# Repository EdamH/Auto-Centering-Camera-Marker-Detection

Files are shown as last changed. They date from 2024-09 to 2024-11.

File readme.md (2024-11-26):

# Development of an Intelligent Camera System for the Detection & Automatic Centering of Markers

## 1- Brief Description : 

The motivation behind this project stems from the need to enhance the safety, efficiency,
and accuracy of power line inspections. Traditional methods, which often involve
manned helicopters, are not only costly and time-consuming but also pose significant
risks to human operators. By automating the detection and centering processes
using advanced algorithms, embedded systems, and wireless communication,
this project aims to offer a more reliable and scalable solution that can adapt to various
geographical and environmental conditions.

## 2- Requirements and coverage :

- [x] The system must detect markers in images and their offset from the desired position (e.g., using an algorithm like Canny edge detection)
- [x] The system must include an embedded controller to correct the camera position across all three axes (e.g., using servo motors)
- [x] The system must support wireless communication of the original image and correction parameters (e.g., using Bluetooth Low Energy boards)
- [x] The system must implement energy management for all components (e.g., utilizing solar panels or rechargeable batteries)
- [x] The system must feature an Android app to display images and correction parameters.
- [x] The system must be printed onto a PCB card.
- [x] The camera support allowing the camera to turn around all three axes must be modeled and printed.

## 3- The Technological Stack :

Currently, the project uses the following technologies:

- Raspberry Pi 4 (single-board computer)
- ESP32 (Wi-Fi and Bluetooth microcontroller)
- Power Management Unit (PMU)
- Pi Camera (camera module for Raspberry Pi)
- Batteries and Solar Panels (for power management)
- Altium Designer (for PCB design)
- Pi Imager (for creating Raspberry Pi SD cards)
- Arduino IDE (for microcontroller programming)
- VNC Viewer (for remote desktop control)
- Fusion 360 (for 3D design and manufacturing)
- Blender (for 3D graphics and modeling)
- Python (for computer vision algorithm development)
- VS Code (source code editor)
- OpenCV (computer vision library)
- Flutter (UI development kit)
- Dart (for mobile app development )

## 4- Solution Architecture :

### 4.1- Hardware Architecture

#### Overview

##### Data Flow
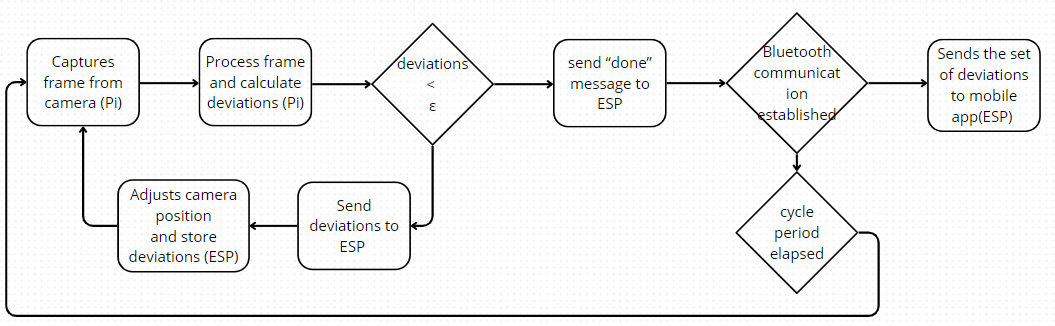
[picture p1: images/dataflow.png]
Data flow
  
- The data flow diagram represents the core process of the project. The process begins with the camera capturing a frame, which is processed by the Raspberry Pi 4 using a computer vision algorithm. This algorithm calculates deviations along three axes.
- These deviations are compared against a predefined epsilon value. If any deviation exceeds the epsilon threshold, the values are transmitted to the ESP32.
- The ESP32 stores the deviations and commands the servo motors to adjust the camera’s position to the desired alignment. 
- This cycle repeats until all deviations fall within the epsilon threshold.
- When the system meets this condition, it waits for the next cycle to begin.
- If a Bluetooth connection is established with a mobile device, the set of deviations is transmitted to the mobile application for logging and monitoring.

##### Current Flow
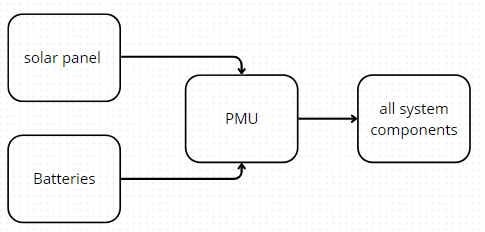
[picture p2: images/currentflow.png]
Current flow
  
- The current flow diagram shows the power distribution in the project.
- Batteries provide power to the entire system, managed by the Power Management Unit (PMU).
- The PMU ensures stable voltage and current delivery to all components.
- It also manages the battery charging process using solar panels, while protecting against overcharging, overdischarging, and short circuits, ensuring safe and efficient operation of the system.

## 4.2- Software Architecture

### Computer Vision
- The approach overview is depicted in Figure 3.3, which outlines the steps taken to provide the necessary offsets to the system.
- The camera captures frames, which are processed by the computer vision algorithm on the Raspberry Pi to calculate deviations from the desired position across three axes.

<div style="text-align: center;">
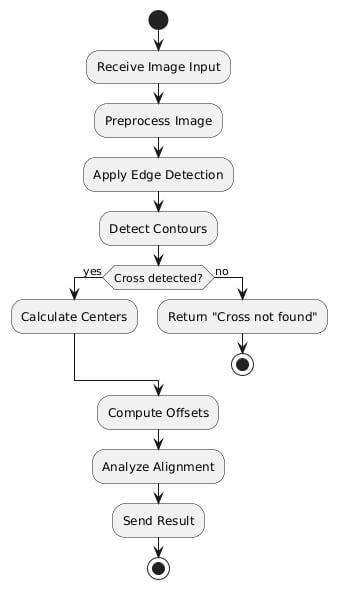
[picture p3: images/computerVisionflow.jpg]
Computer Vision
    
</div>

## 3D Modeling :

This section highlights the various components we modeled for our solution. Since the mechanical aspect of the project was not the main focus, we do not go into detail on the technical drawings.

- **Figure 4.2.1** – Full Gimbal: A complete view of the gimbal designed to hold the camera.
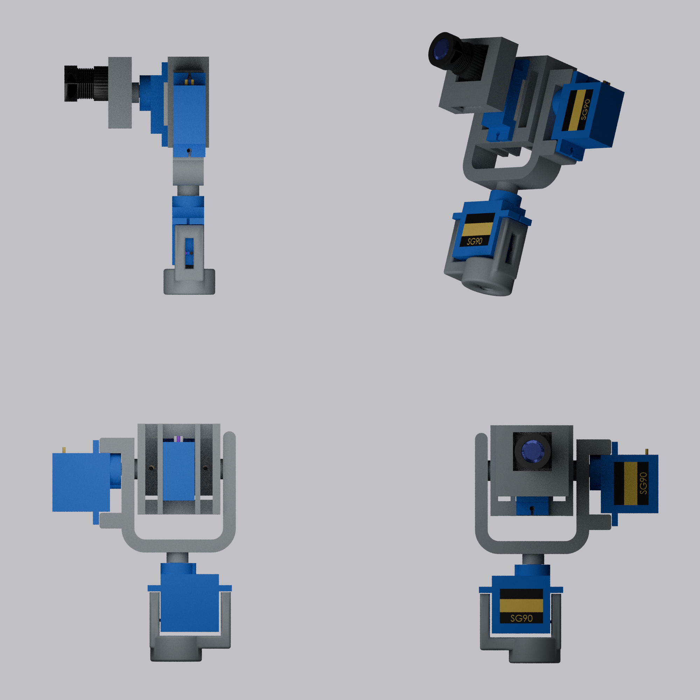
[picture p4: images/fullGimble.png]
Full Solution
  
- **Figure 4.2.2** – Unmounted Full Gimbal: A view of the gimbal when disassembled.
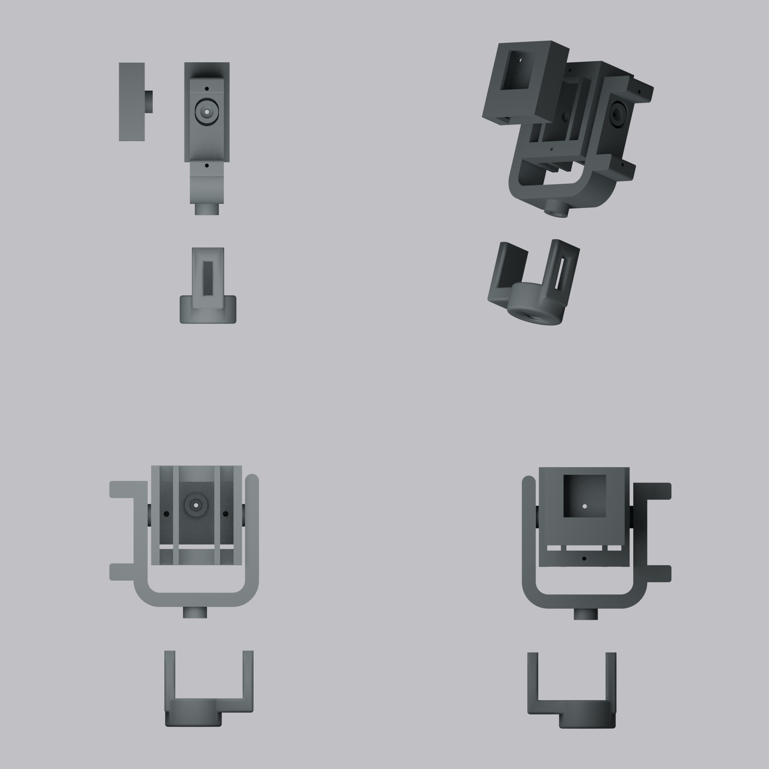
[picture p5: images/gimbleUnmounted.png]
3D model
  
- **Figure 4.2.3** – Battery Holder: A custom-designed holder for securing the batteries that power the system.
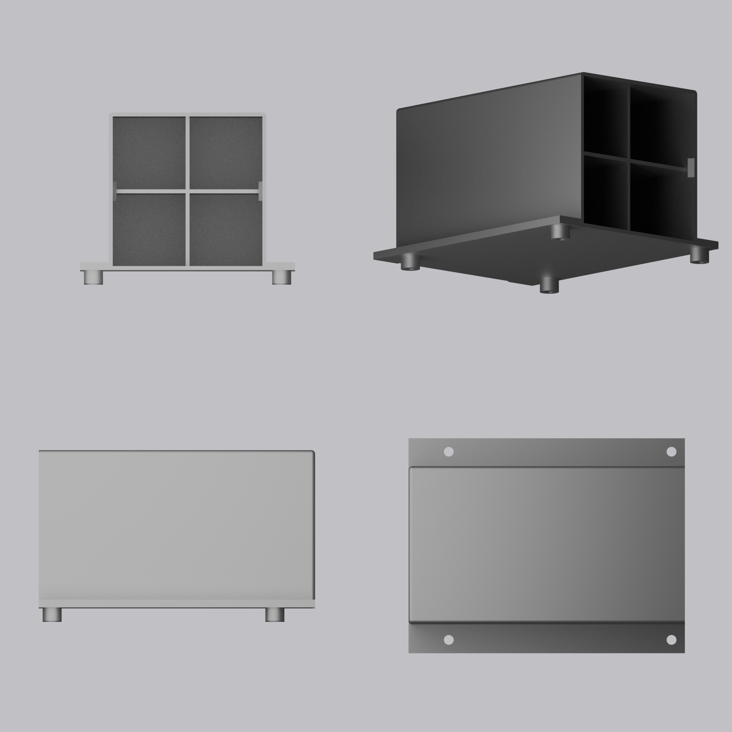
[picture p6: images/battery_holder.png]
Battery Holder
  

## 5- Embedded System :

## Strategies for Power Efficiency

### Manual Sleep Mode Implementation
The Raspberry Pi 4 does not have a built-in sleep mode, so a manual solution was implemented. This involves powering on the Raspberry Pi, performing calculations and camera alignment, scheduling the next boot, and then shutting down the system. This approach allows a 2.4 Ah battery to support approximately 13 hours of operation, effectively doubling the battery life.

### Integrating ESP8266 to Manage Raspberry Pi Power Usage
To further optimize power consumption, the ESP8266 was integrated as a secondary microcontroller. It consumes roughly one-tenth of the power used by the Raspberry Pi in power-off mode, allowing the ESP8266 to control the power to the Raspberry Pi and extending battery life to approximately 60 hours with the same battery.

## Raspberry Pi Issues and Implemented Solutions

### Instability in PWM Signal
The PWM signal generated by the Raspberry Pi was unstable, causing jitter in the servos. The ESP8266 was used to drive the servos, providing a more stable PWM signal.

### Transition to ESP32 for Bluetooth Communication
Bluetooth communication was challenging with the Raspberry Pi, so the ESP32 was chosen for its integrated Bluetooth capabilities and lower power consumption, enabling efficient data exchange with the mobile app.

## Design of Power Management Unit

### Schematic
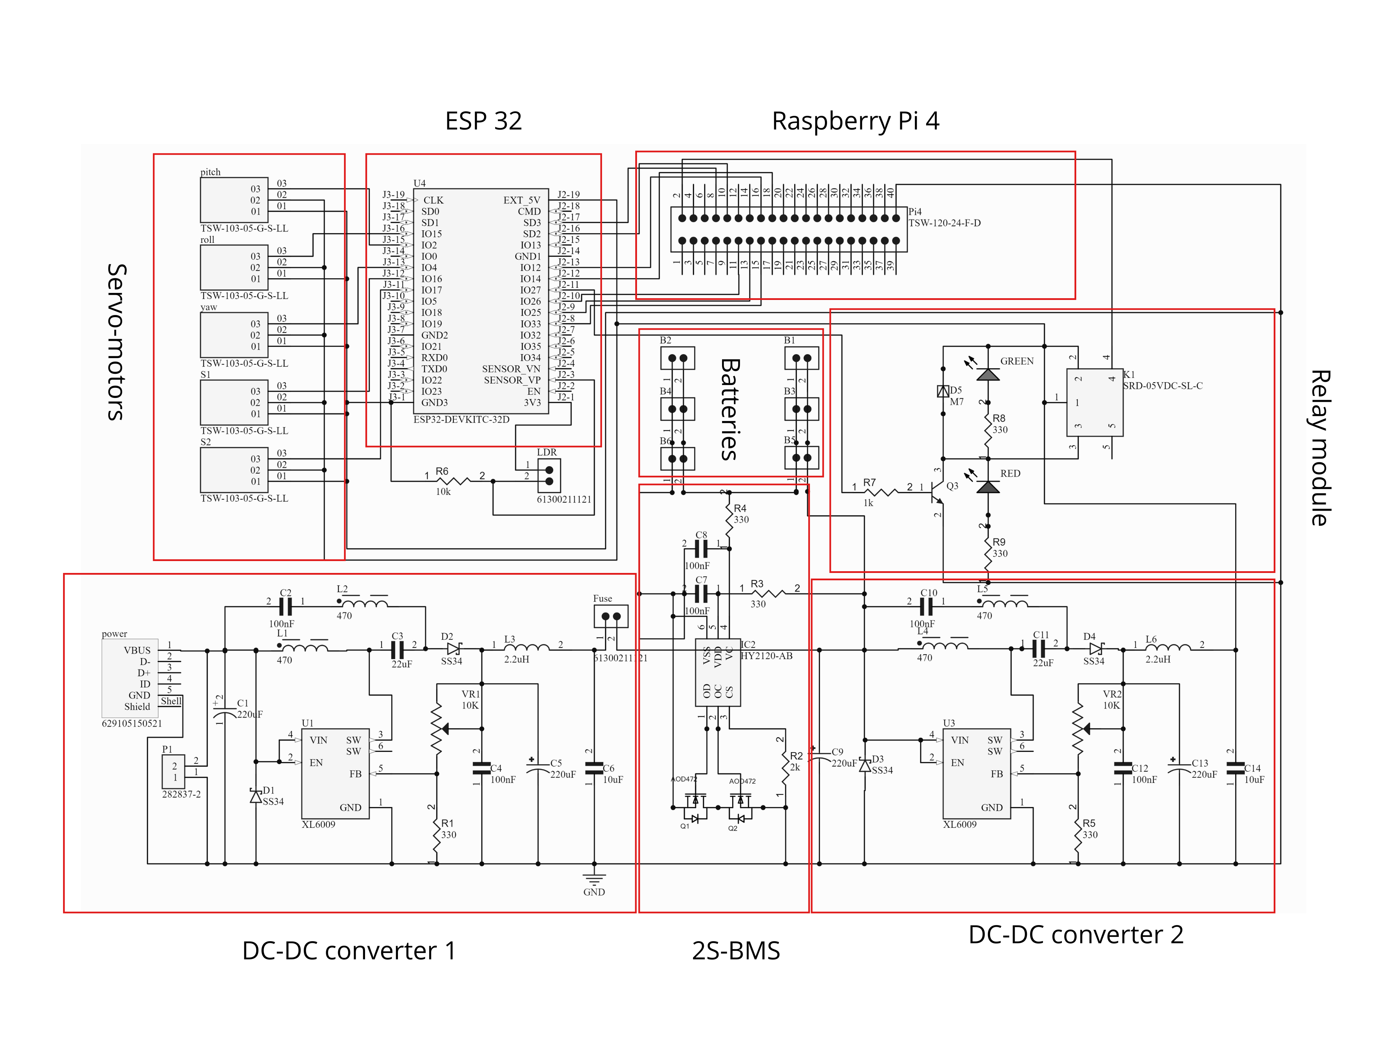
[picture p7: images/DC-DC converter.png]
Power Management Schematic


The schematic includes:
- **DC-DC Converter**: Stabilizes charging voltage at 8.4V and supplies a consistent 5V to the Raspberry Pi and other components.
- **Battery Management System (BMS)**: Controls charging and discharging, prevents overcharging and overdischarging, and ensures voltage balancing.

### PCB
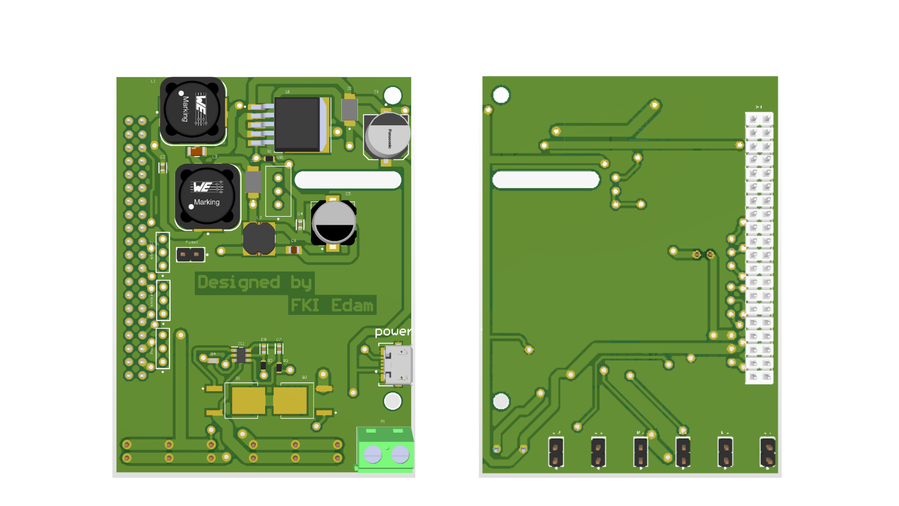
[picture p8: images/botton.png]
Bottom PCB
  
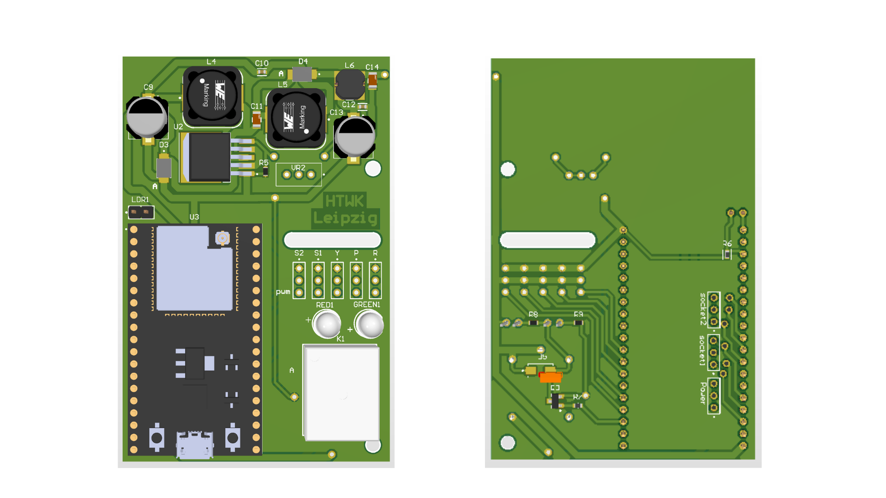
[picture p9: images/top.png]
Top PCB
  
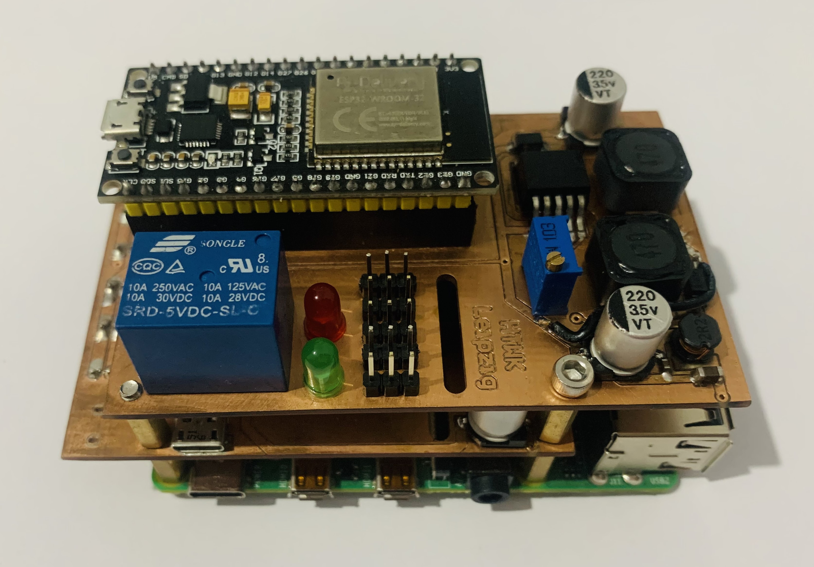
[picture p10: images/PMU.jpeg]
Manufactured PCB


## Energy Consumption

### System Cycle
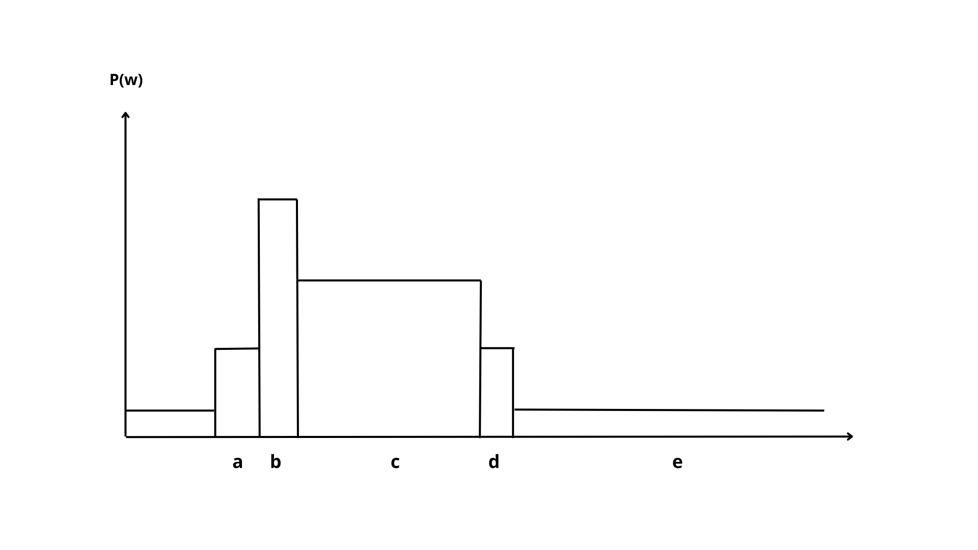
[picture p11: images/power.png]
Power Consumption Cycle


| Component | Energy Consumption | Duration |
|---|---|---|
| Raspberry Pi 4 | At Shut Down: 250mA | 60s |
| | At Processing: 600mA | |
| | At Booting: 1A | |
| ESP32 | At Idle: 20mA | 15 min |
| | At Processing: 80mA | |
| PMU | 20mA | 15 min |
| Servo Motor | 0.1A | 4s |
| Camera | 0.1A | 4s |

### Battery Life
Average power consumption calculated to be approximately 0.7W, resulting in an autonomy of 25h 22min with the existing battery setup. A more powerful solar panel will be needed for full recharging.

### Solar Panel
Initially used a 50W, 17V solar panel, but switched to smaller solar cells for size efficiency while maintaining sufficient power for battery recharging.

## Communication Between ESP-32 and Raspberry Pi 4

### Explored Protocols
- **SPI**: High data rate, master/slave configuration.
- **UART**: Simple, peer-to-peer communication.
- **I2C**: Multi-master/slave with two lines.
- **MQTT**: Lightweight, suitable for IoT applications.

### Selected Protocol: Serial (UART)
After evaluation, UART was chosen for its simplicity and sufficient data rate, allowing either device to initiate communication.

### Implementation Details
#### Hardware Setup
- **UART Communication Lines**: 
  - Pi TX Pin → ESP32 UART1 RX Pin
  - Pi RX Pin → ESP32 UART1 TX Pin
- **Interrupt Line**: 
  - Pi GPIO Pin → ESP32 GPIO Pin
- **Ground Connection**: 
  - GND pins connected for a common ground reference.

#### Protocol Workflow
<div style="text-align: center;">
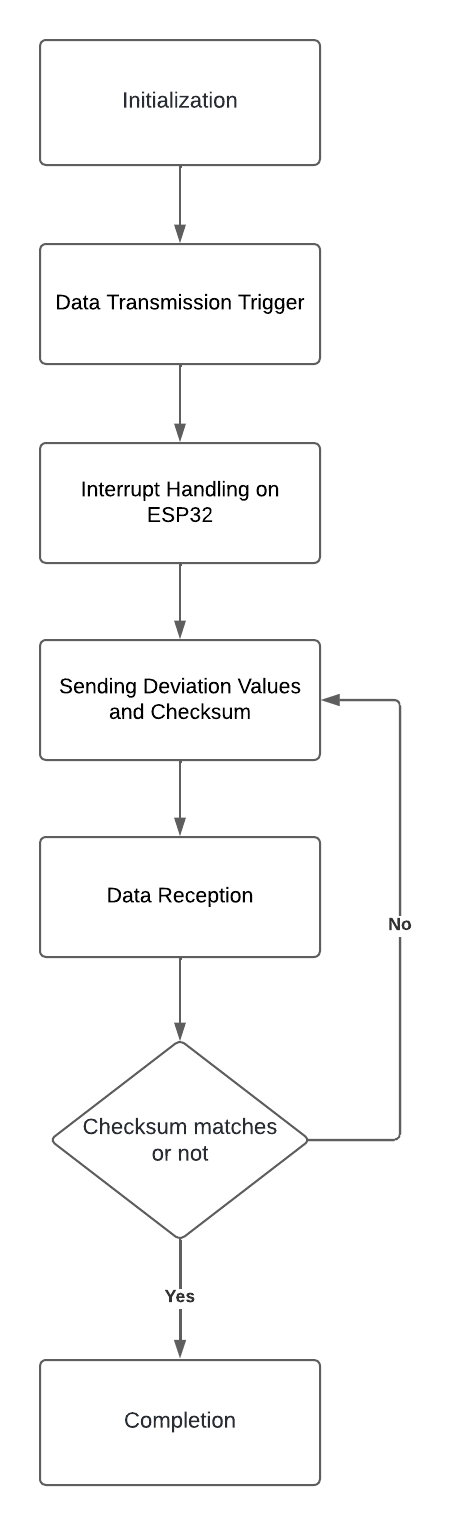
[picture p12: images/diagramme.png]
Protocol Workflow
    
</div>

The communication involves initialization, data transmission triggers, and acknowledgment of received data between the Raspberry Pi and ESP32.

## 6- Computer Vision :

## Cross Detection

### Approach Overview
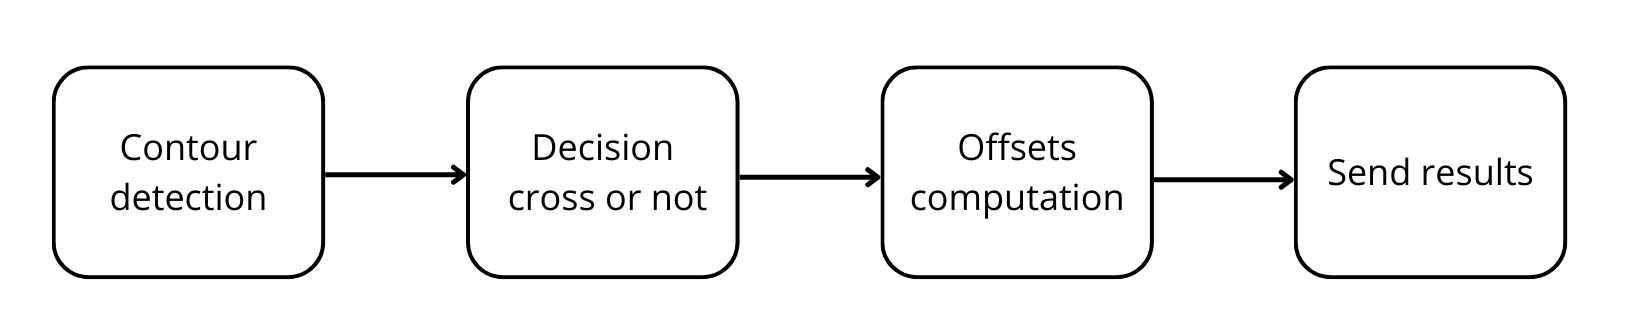
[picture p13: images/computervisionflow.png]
Approach Overview


### Contour Detection
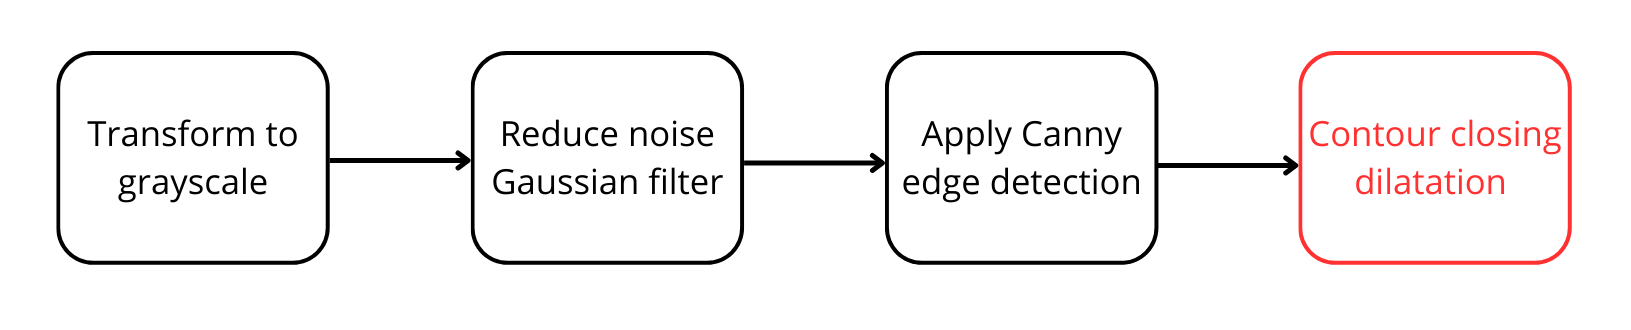
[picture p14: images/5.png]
Contour Detection Pipeline


In this step, the image is loaded in grayscale to simplify data and enhance edge detection. A Gaussian blur filter is applied to reduce noise, followed by Canny edge detection with optimal threshold values to filter weak edges while retaining strong ones. Finally, contours are extracted from the edge-detected image.

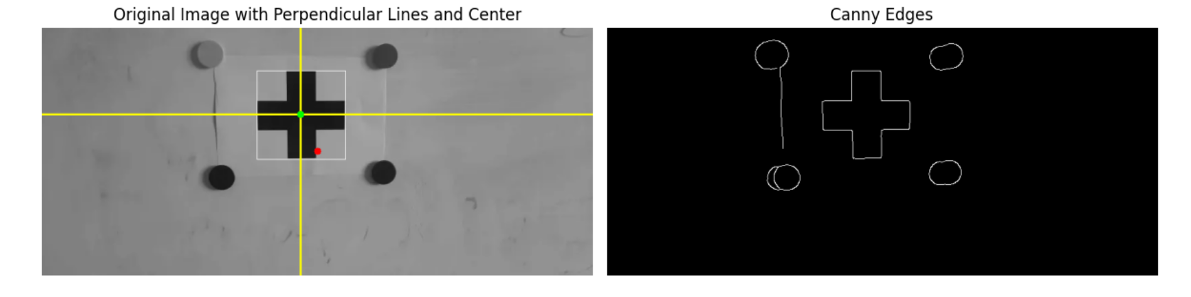
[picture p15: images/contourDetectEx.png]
Example of Cross Detection


To address discontinuities in the contours, dilation is applied to the edge-detected image, expanding the boundaries of detected edges.

### Decision About the Cross
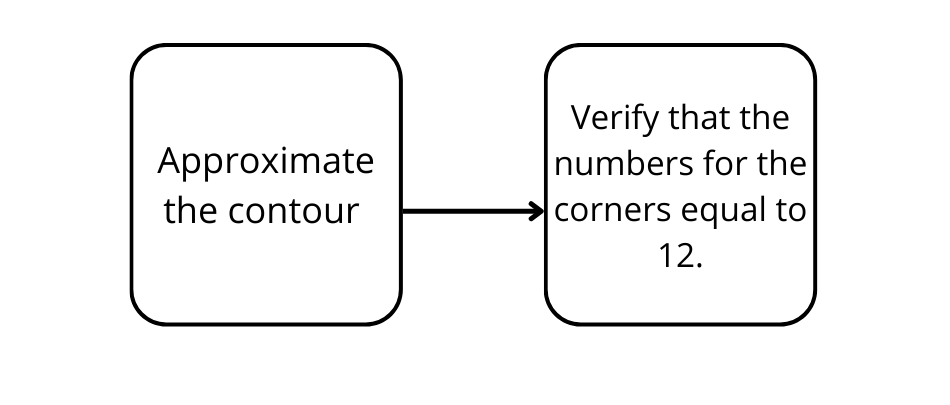
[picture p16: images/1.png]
Decision Pipeline


The detected contours are simplified and approximated to polygons with fewer vertices using a specified epsilon parameter for accuracy. Contours with 12 corners are filtered to identify the cross shape, and a bounding box is determined to convert offsets from pixels to meters.

### Offsets Computation
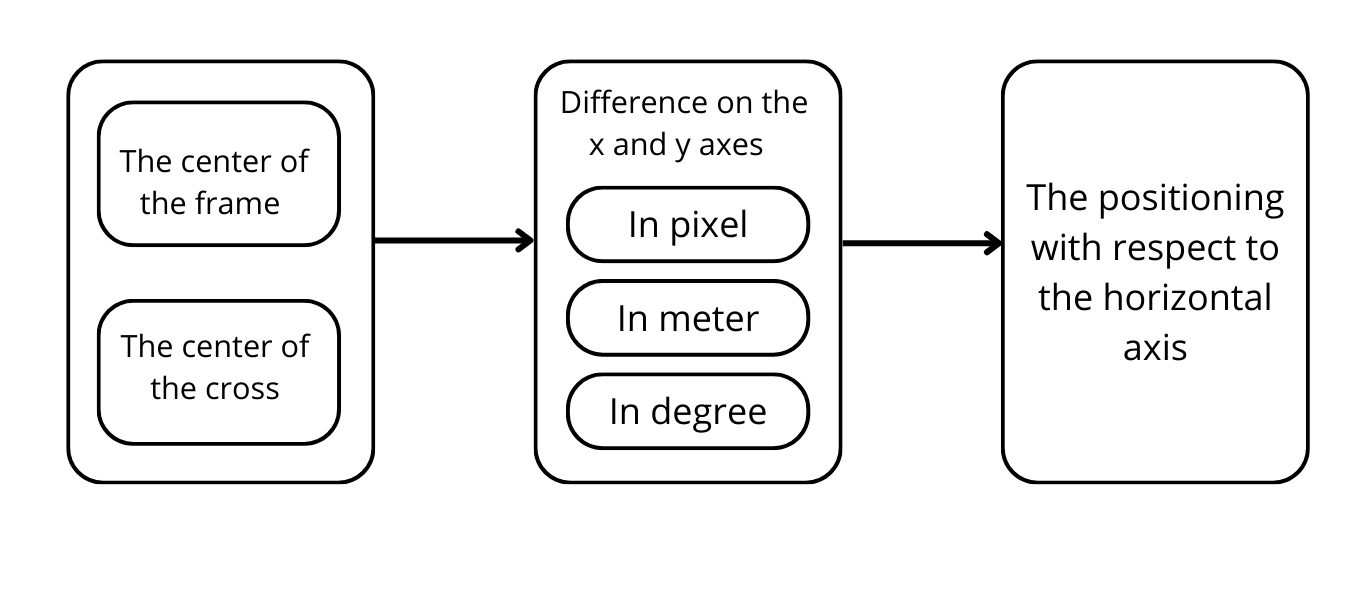
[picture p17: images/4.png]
Offsets Computation Pipeline


Offsets for the servo motors are calculated by determining the centers of the image and the cross. The difference in pixel coordinates on the x and y axes is computed. Using the cross width, a ratio for converting pixel measurements to physical dimensions is derived, allowing the extraction of angles for servo-motor adjustments.

Additionally, the alignment of the cross is considered by calculating its deviation from the horizontal axis by drawing a line between the closest detected corners and calculating the angle relative to the axis.

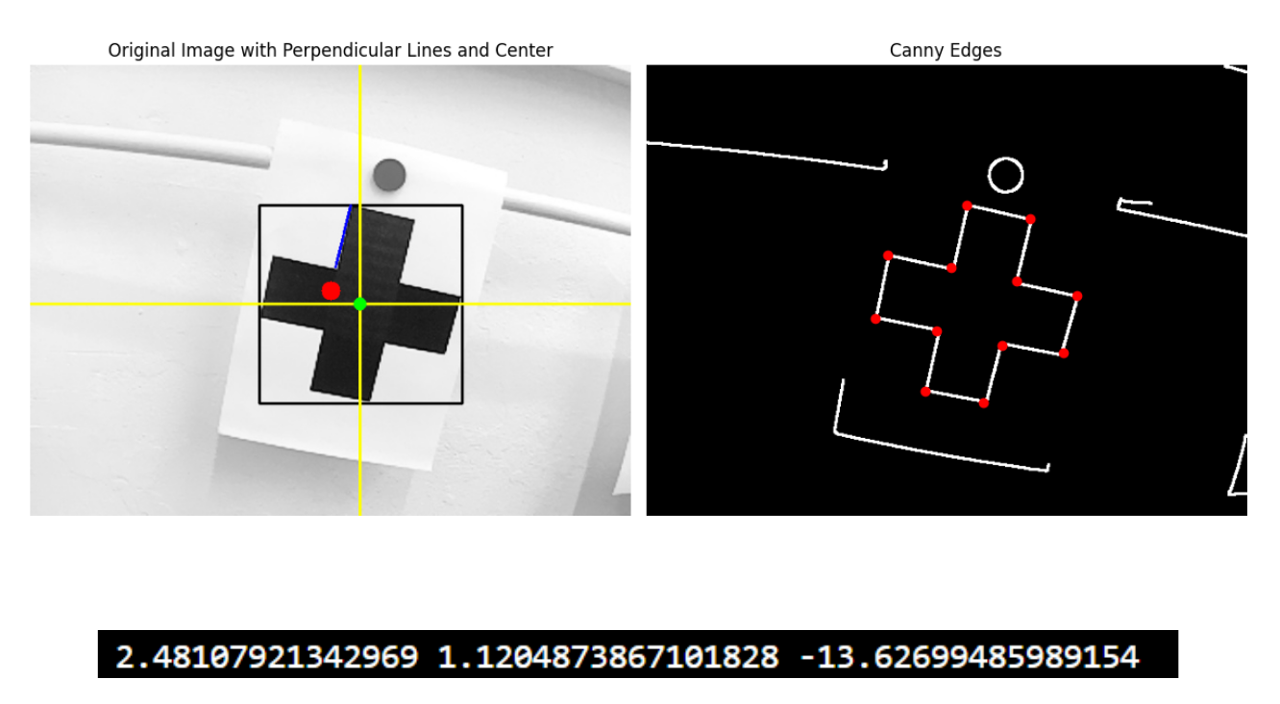
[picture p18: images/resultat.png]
Example of Result


### Approach Limits
The algorithm can theoretically detect a cross with an opacity level of 6%, but in practice, it achieves around 25%.

## Mathematical Approach :

### Overview
Let (X, Y, Z) be the orthonormal reference attached to the camera, where Z is vertical and X points at the detected object. The orientations the camera must adjust to center the detected object are represented as θX, θY, and θZ.

The algorithm follows these steps:
1. The distance D between the camera and the detected object (cross or pole) is input.
2. The width of the item in pixels is computed to approximate the pixel-to-meter ratio.
3. Offsets along the vertical and horizontal axes are calculated, yielding rotations θZ and θY around the Z and Y axes.
4. Rotation along the θX axis is determined by comparing the object's orientation relative to the horizontal axis.

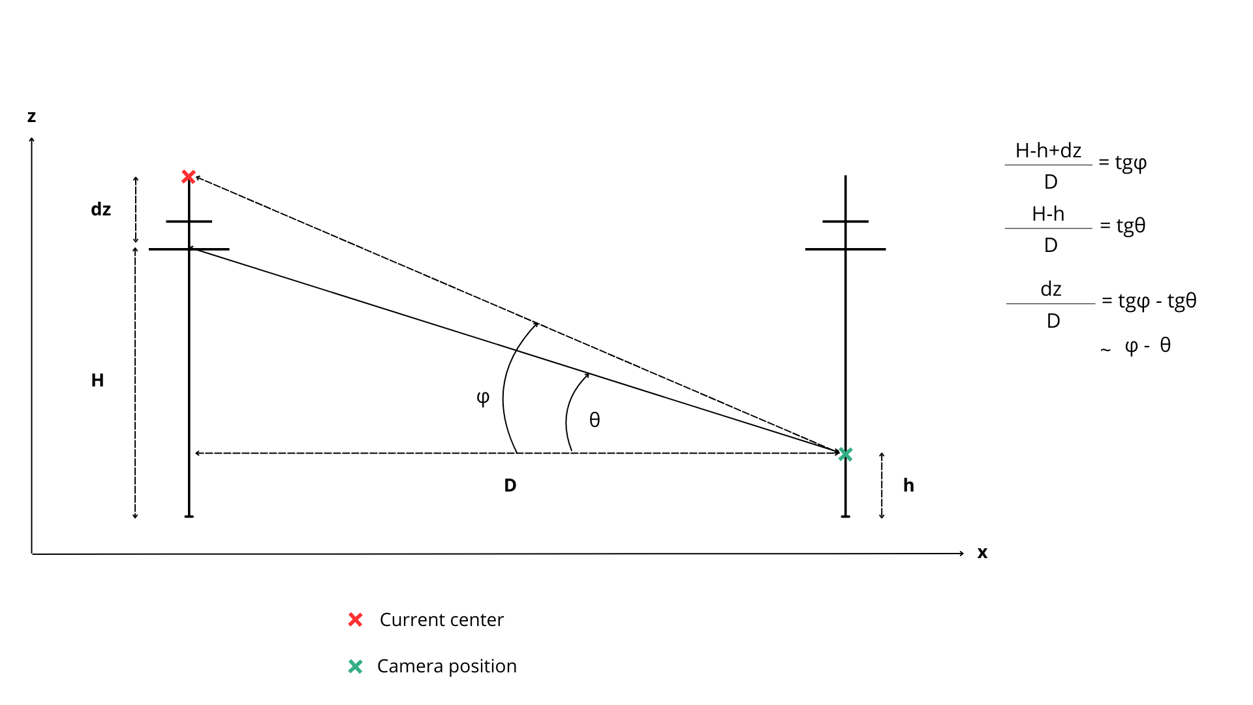
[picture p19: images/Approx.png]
Visual Representation of the Problem for θY


### Validity of the Approximation
To reduce computational load, the approximation tan(θ) ≈ θ is used when θ approaches 0. Analysis shows that the error is under 0.01 for θ < 0.31 and under 0.1 for θ < 0.63, ensuring that deviations remain manageable for the project's conditions.

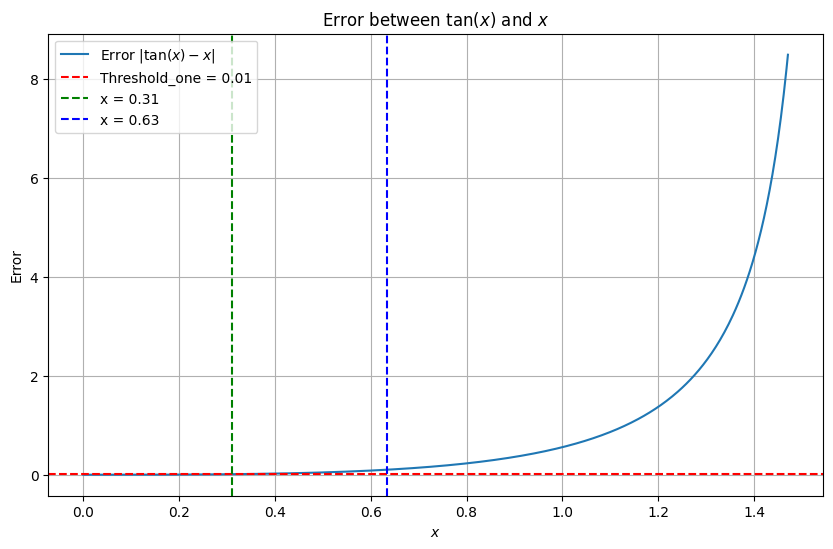
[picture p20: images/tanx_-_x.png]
Absolute Error |tan(θ) - θ|


## Bluetooth Communication for Mobile Application :

### Bluetooth Overview
Bluetooth is a wireless communication protocol designed for short-range data exchange between devices. Operating in the 2.4 GHz ISM band, it supports both point-to-point and point-to-multipoint connections. Bluetooth is widely used in consumer electronics for applications such as wireless audio, file transfers, and peripheral connections.

### Use Case and Implementation
In this system, Bluetooth facilitates communication between the ESP-32 and a mobile application, allowing users to interact via smartphones. Key features include remote control, status monitoring, and notifications.

The ESP-32 is configured to operate in Bluetooth Low Energy (BLE) mode, chosen for its low power consumption, essential for maintaining battery life in mobile applications. The mobile application connects to the ESP-32, enabling command transmission and real-time updates.

This wireless communication layer significantly enhances user experience, providing a convenient and accessible interface for system interaction without physical connections.

### Mobile Application
The mobile application is developed using Flutter and Dart, offering a cross-platform solution for both Android and iOS. Flutter enables the creation of visually appealing, high-performance interfaces, while Dart provides flexibility for handling Bluetooth communication and real-time data processing. This combination ensures a responsive and seamless user experience.

For Bluetooth communication, the SerialBT library is implemented on the ESP-32, providing a reliable method for data transmission between the system and the mobile app. SerialBT supports Bluetooth Classic profiles, ensuring compatibility and stability. This setup allows the ESP-32 to transmit real-time data, including cycle details and measurement offsets, directly to the app.

Once a stable Bluetooth connection is established, the system enters a critical phase where real-time data from the current cycle is transmitted. The ESP-32 provides detailed cycle information, including offsets, measurement indices, and current positions.

The mobile app processes incoming data to compute and display precise timestamps for each measurement, calculating the difference between the current time and the start of the cycle. This allows for accurate iteration through remaining measurements and the creation of a timeline.

In addition to real-time data presentation, the app generates a histogram visualizing the distribution of measurements over time. This provides users with accurate, time-stamped information and insights into the temporal distribution of measurements within each cycle.

The user interface prioritizes clarity and usability, focusing on presenting essential data in an intuitive format.

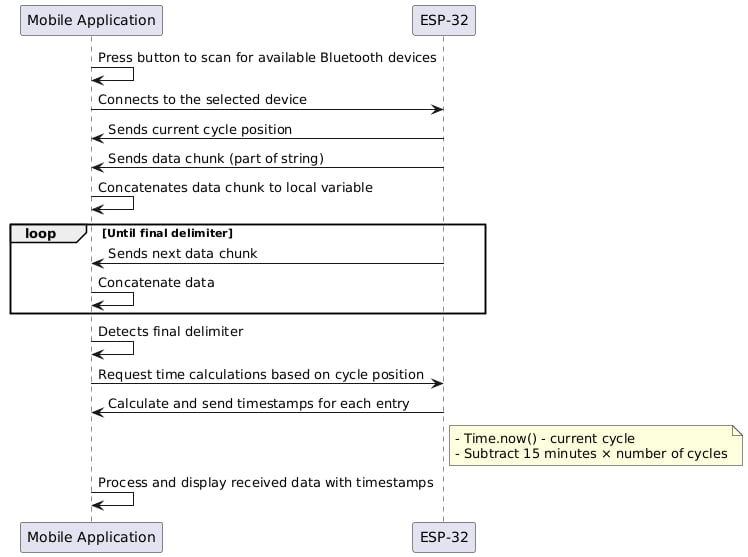
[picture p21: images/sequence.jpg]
Bluetooth Sequence


### Screenshots of the Application
<div style="display: flex; justify-content: space-around;">
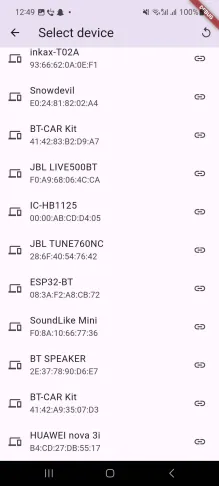
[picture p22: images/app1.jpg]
First Page
    
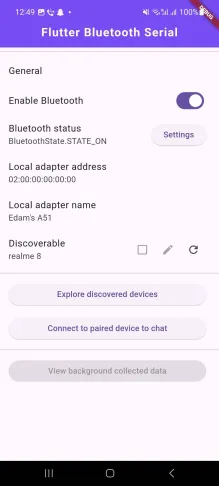
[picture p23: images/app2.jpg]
Paired Devices
    
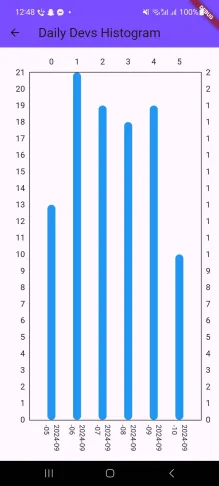
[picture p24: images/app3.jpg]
Measurements
    
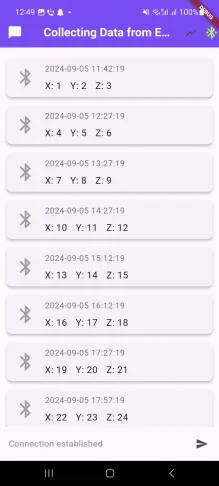
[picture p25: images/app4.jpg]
Histogram
    
</div>

## Collaborators
<a href="https://https://github.com/EdamH/Auto-Centering-Camera-Marker-Detection/graphs/contributors">
    
  
</a>

# Feel free to contribute!

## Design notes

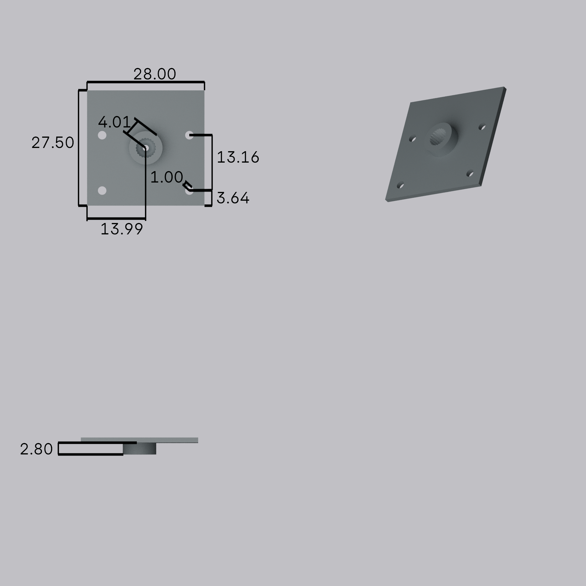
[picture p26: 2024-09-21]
images/cameraCaseRear.png

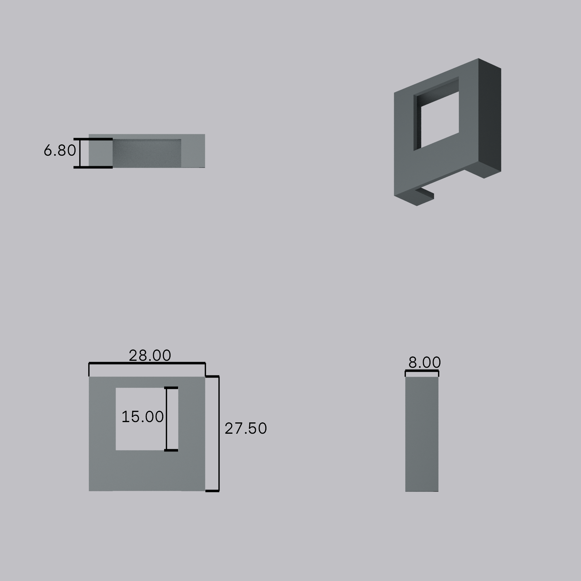
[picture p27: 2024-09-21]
images/cameraCase.png

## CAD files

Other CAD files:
3D Model/Cover v1.f3d
3D Model/Spacer v2.f3d
3D Model/battery_holder v3.f3d

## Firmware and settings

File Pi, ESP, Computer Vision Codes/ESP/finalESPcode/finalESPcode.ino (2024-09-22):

#include <HardwareSerial.h>  // Library to use hardware serial communication
#include <ESP32Servo.h>      // Library to control servos on ESP32
#include "BluetoothSerial.h" // Library for Bluetooth communication

BluetoothSerial SerialBT;    // Bluetooth object
String device_name = "ESP32-BT"; // Bluetooth device name

int Sample_number = 0;       // Counter for the number of samples processed
int t_cycle = 900000;        // Time cycle (15 minutes) in milliseconds

long tic = millis();         // Start time of the cycle

String dataset;              // String to store dataset (servo positions)

bool a = 1, b = 0, c = 0;    // Flags for the power-off sequence
long st;                     // Start time for power-off
int d;                       // Time remaining after power-off

// Pin definitions
#define relay 33             // Relay control pin (used to power Pi4)
#define s_interrupt 25       // Interrupt pin for servo control
#define p_interrupt 14       // Interrupt pin for power control

// Pins for hardware serial communication
#define RX 9
#define TX 10

Servo servo1, servo2, servo3; // Servo objects

// Initial servo positions
int X = 100, Y = 90, Z = 80;  

bool calculating = 1;        // Flag to indicate if calculations are ongoing
int delta = 0;               // Time spent in a cycle

HardwareSerial HSerial(1);   // Hardware serial object (for UART1)

volatile bool servo = false; // Flag set by the interrupt for servo control
volatile bool power = false; // Flag set by the interrupt for power control

// Interrupt handler for servo control
void IRAM_ATTR servo_write() {
  servo = true;  // Set a flag to indicate the servo interrupt event
}

// Interrupt handler for power control
void IRAM_ATTR power_off() {
  power = true;  // Set a flag to indicate the power interrupt event
}

void setup() {
  SerialBT.begin(device_name);         // Initialize Bluetooth with the device name
  pinMode(relay, OUTPUT);              // Set relay pin as output
  attachInterrupt(p_interrupt, power_off, RISING); // Attach interrupt for power control
  attachInterrupt(s_interrupt, servo_write, RISING); // Attach interrupt for servo control
  Serial.begin(115200);                // Initialize serial communication
  HSerial.begin(9600, SERIAL_8N1, RX, TX); // Initialize hardware serial for communication

  // Setup servos with a 50 Hz PWM signal and attach them to corresponding pins
  servo1.setPeriodHertz(50);
  servo1.attach(17, 550, 2500);        // Attach servo1 to pin 17
  servo2.setPeriodHertz(50);
  servo2.attach(16, 550, 2500);        // Attach servo2 to pin 16
  servo3.setPeriodHertz(50);
  servo3.attach(5, 550, 2500);         // Attach servo3 to pin 5

  // Write initial servo positions
  servo1.write(X);
  servo2.write(Y);
  servo3.write(Z);

  Serial.println(millis() - tic);      // Print time since the start of the program
}

void loop() {
  // If the system is in calculating mode, process servo adjustments
  if (calculating) {
    digitalWrite(relay, HIGH);         // Turn on the relay to power external devices

    // Check if the servo interrupt flag was set
    if (servo) {
      // Check if data is available on the hardware serial
      if (HSerial.available()) {
        Serial.println("receiving");
        String data = HSerial.readStringUntil('\n');  // Read incoming data until newline character
        int ang1 = 0, ang2 = 0, ang3 = 0, s = 0;      // Variables for servo angles and checksum
        Serial.println(data);

        // Parse the angles and checksum from the received data
        sscanf(data.c_str(), "%d,%d,%d,%d", &ang1, &ang2, &ang3, &s);

        Serial.print("servoN°1=");
        Serial.println(ang1);
        Serial.print("servoN°2=");
        Serial.println(ang2);
        Serial.print("servoN°3=");
        Serial.println(ang3);

        // Check the integrity of the received data
        int h = ang1 + 2 * ang2 + 3 * ang3;
        if (h - s == 0) { // If checksum is correct
          // Adjust servo positions
          X = X - ang1;
          Y = Y - ang2;
          Z = Z - ang3;

          Serial.print("x=");
          Serial.println(X);
          Serial.print("Y=");
          Serial.println(Y);
          Serial.print("Z=");
          Serial.println(Z);

          // Update servo positions if within valid range
          if (X > 60) {
            servo1.write(X);
          } else {
            Serial.println("x<60");
          }

          servo2.write(Y);

          if (Z > 60) {
            servo3.write(Z);
          } else {
            Serial.println("z<60");
          }

          // Send acknowledgment to the sender
          HSerial.println("received");
          Sample_number++;

          // Update dataset with the new positions
          String rotation = "";
          if (dataset.length() == 0) {
            rotation = String(X) + "," + String(Y) + "," + String(Z) + "\r";
          } else {
            rotation = "|" + String(X) + "," + String(Y) + "," + String(Z) + "\r";
          }
          dataset = dataset + rotation;

          // Clear the input buffer
          HSerial.readStringUntil('\n');
        } else {  // If checksum is incorrect
          HSerial.println("resend");
        }
      } else {  // If no serial data is available
        Serial.println("serial not available");
        HSerial.println("resend");
      }

      servo = false;  // Reset the servo interrupt flag
      HSerial.readStringUntil('\n');  // Clear any remaining data
    }

    // Check if the power interrupt flag was set
    if (power) {
      Serial.println("shutting down");
      calculating = 0;  // Stop calculations
      if (a) {          // First stage of power-off sequence
        st = millis();
        a = 0;
        b = 1;
      }
      if (b) {          // Wait for 4 seconds before powering off
        if (millis() - st >= 4000) {
          digitalWrite(relay, LOW);  // Turn off the relay to cut power
          delta = millis() - tic;    // Calculate the time spent in this cycle
          Serial.print("delta =");
          Serial.println(delta);
          d = t_cycle - delta;       // Calculate the remaining time for the cycle
          b = 0;
          c = 1;
          st = millis();
        }
      }
      if (c) {          // Wait for the remaining cycle time before restarting
        if (millis() - st >= d) {
          calculating = 1;  // Resume calculations after the cycle
          power = false;    // Reset the power interrupt flag
        }
      }
    }

    // Bluetooth communication: check if data is received via Bluetooth
    if (SerialBT.available()) {
      String incomingData = SerialBT.readStringUntil('\n');
      incomingData.trim();
      Serial.println("Received: " + incomingData);

      // If the received data is "a", send the elapsed time and dataset
      if (incomingData == "a") {
        long t = millis() - tic;  // Calculate the elapsed time
        Serial.println(t);
        String msg = String(t) + "#";  // Send the time

        int len = msg.length();
        char byteArray[len + 1];
        msg.getBytes((unsigned char*)byteArray, len + 1);
        SerialBT.write((uint8_t*)byteArray, len);
        delay(50);

        // Send the dataset of servo rotations
        msg = dataset + "\r";
        len = msg.length();
        char byteArray1[len + 1];
        msg.getBytes((unsigned char*)byteArray1, len + 1);
        SerialBT.write((uint8_t*)byteArray1, len);
      }
    }
  }
}

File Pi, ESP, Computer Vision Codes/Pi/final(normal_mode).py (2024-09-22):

import os
import cv2
import math
import numpy as np
from time import sleep
from itertools import combinations
from picamera2 import Picamera2
import random
import RPi.GPIO as GPIO
import matplotlib.pyplot as plt
import serial

epsilon=1 #the minimum deviatu=ion that can be made by servo-motors

# Initialize a flag to check if data needs to be resent
resend = False

# Initialize the serial connection for communication with another device
ser = serial.Serial('/dev/ttyS0', 9600, timeout=1)

# Set up GPIO pins for controlling hardware (e.g., servos)
GPIO.setmode(GPIO.BCM)
GPIO.setwarnings(False)
GPIO.setup(23, GPIO.OUT)  # Pin for sending data
GPIO.setup(24, GPIO.OUT)  # Pin for power control

def send(ang1, ang2, ang3):
    """
    Send the angles as a formatted message over serial communication.
    """
    message = f"{ang1},{ang2},{ang3},{ang1+2*ang2+3*ang3}\n"  # Create a message with angles
    GPIO.output(23, GPIO.HIGH)  # Signal the start of transmission
    ser.write(message.encode())  # Encode and send the message
    GPIO.output(23, GPIO.LOW)  # Signal the end of transmission
  
def Send(thetaX, thetaY, thetaZ):
    """
    Send the calculated angles and wait for acknowledgment.
    Resend if data is not valid.
    """
    print("Starting transmission")
    while True:
        try:
            line = ''
            send(int(thetaX), int(thetaY), int(thetaZ))  # Send the angles
            sleep(0.3)  # Wait for acknowledgment
            line = ser.readline().decode('utf-8').rstrip()  # Read the response
            print(line)
            if line == "received":
                print("Data received successfully")
                break  # Exit loop if data is received
            elif line == "resend":
                print("Data was not valid, resending...")
                ser.flush()  # Clear serial buffer
            else:
                print(f"Unexpected response: {line}")
                ser.flush()  # Clear serial buffer
        except UnicodeDecodeError:
            print("Failed to decode the received data. It might not be in UTF-8.")
            ser.flush()  # Clear serial buffer
    print("Transmission complete")

def find_central_pixel_of_objects(contours, image):
    """
    Find and return the central pixels of detected objects with 12 corners.
    """
    central_pixels = []
    cross_widths = []
    for contour in contours:
        # Approximate the contour for better shape representation
        epsilon = 0.02 * cv2.arcLength(contour, True)
        approx = cv2.approxPolyDP(contour, epsilon, True)

        # Check if the approximated contour has exactly 12 corners
        if len(approx) == 12:
            M = cv2.moments(contour)  # Calculate moments for central pixel
            if M['m00'] != 0:
                cX = int(M['m10'] / M['m00'])
                cY = int(M['m01'] / M['m00'])
                central_pixels.append((cX, cY))

                # Calculate bounding box dimensions
                x, y, w, h = cv2.boundingRect(contour)
                cross_widths.append(w)

                # Draw bounding rectangle and center point on the image
                cv2.rectangle(image, (x, y), (x + w, y + h), (0, 255, 0), 2)
                cv2.circle(image, (cX, cY), 5, (255, 0, 0), -1)  # Center point in blue

    return image, central_pixels, cross_widths

def draw_perpendicular_lines(image, point):
    """
    Draw vertical and horizontal lines through a given point on the image.
    """
    height, width = image.shape[:2]
    cX, cY = point

    # Draw vertical and horizontal lines
    cv2.line(image, (cX, 0), (cX, height), (0, 255, 255), 2)  # Yellow vertical line
    cv2.line(image, (0, cY), (width, cY), (0, 255, 255), 2)  # Yellow horizontal line

def find_closest_corners(corners):
    """
    Find and return the two closest corners from a list of corners.
    """
    if len(corners) < 2:
        return None, None
    sorted_corners = sorted(corners, key=lambda corner: corner[1])  # Sort by y-coordinate

    min_distance = float('inf')
    x1, y1 = sorted_corners[0]
    closest_corner = None

    for (x2, y2) in sorted_corners[1:4]:  # Check only the next three corners
        distance = np.sqrt((x2 - x1) ** 2 + (y2 - y1) ** 2)  # Calculate distance
        if distance < min_distance:
            min_distance = distance
            closest_corner = (x2, y2)

    return sorted_corners[0], closest_corner

def find_corners_of_objects(contours):
    """
    Find and return the corners of detected objects with 12 corners.
    """
    corners = []
    for contour in contours:
        epsilon = 0.03 * cv2.arcLength(contour, True)  # Set approximation accuracy
        approx = cv2.approxPolyDP(contour, epsilon, True)

        # Check if the approximated contour has exactly 12 corners
        if len(approx) == 12:
            for point in approx:
                corners.append(tuple(point[0]))  # Add corners to the list
    return corners
def process_image(image_path, plot=False):
    # Load the image in grayscale (assuming image_path is already a BGR image)
    image = cv2.cvtColor(image_path, cv2.COLOR_BGR2GRAY)
    
    # Apply Gaussian Blur to reduce noise in the image
    blurred_image = cv2.GaussianBlur(image, (5, 5), 1.4)

    # Apply Canny edge detection to identify edges in the image
    edges = cv2.Canny(blurred_image, 50, 150)
    
    # Dilate the edges to close gaps and make contours more defined
    kernel = np.ones((3, 3), np.uint8)
    edges = cv2.dilate(edges, kernel, iterations=1)
    
    # Find contours in the edge-detected image
    contours, _ = cv2.findContours(edges, cv2.RETR_EXTERNAL, cv2.CHAIN_APPROX_SIMPLE)

    # Identify the central pixel coordinates of detected objects with 12 corners
    image, central_pixels, cross_widths = find_central_pixel_of_objects(contours, image)

    # Create a color image from the grayscale image for drawing
    color_image = cv2.cvtColor(image, cv2.COLOR_GRAY2BGR)
    
    # Calculate the center coordinates of the image
    height, width = image.shape
    center_image = (width // 2, height // 2)

    # Draw a red circle at the center of the image
    cv2.circle(color_image, center_image, 10, (0, 0, 255), -1)  
    
    # Find corners of the detected objects
    corners = find_corners_of_objects(contours)

    # Identify the two closest corners to each other
    corner1, corner2 = find_closest_corners(corners)

    # If two corners are found, draw a line between them and calculate the angle
    if corner1 is not None and corner2 is not None:
        cv2.line(color_image, corner1, corner2, (255, 0, 0), 2)  # Draw a line in blue

        # Calculate the angle of the line with respect to the horizontal axis
        dx = corner2[0] - corner1[0]
        dy = corner2[1] - corner1[1]
        angle_radians = np.arctan2(dy, dx)
        angle_degrees = np.abs(np.degrees(angle_radians))
        print("angle_degrees= ", angle_degrees)
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

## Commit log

2024-09-22 PMU_V3 : Schematics and PCB Design
    [Bottom.SchDoc, Bottom_PCB.PcbDoc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]
2024-09-22 Final ESP32 code
    The code controls servo motors and manages power cycles using an ESP32, which communicates with a Raspberry Pi 4 via UART and a mobile app via Bluetooth. It receives servo angle commands from the Pi,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
2024-09-22 remaining 3D models and esp and PI4 codes
    [Cover v1.f3d, Spacer v2.f3d, battery_holder v3.f3d]
